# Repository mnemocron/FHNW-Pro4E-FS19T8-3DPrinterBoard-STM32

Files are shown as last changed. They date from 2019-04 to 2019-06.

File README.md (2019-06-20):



# FHNW-Pro4E-FS19T8-3DPrinterBoard-STM32

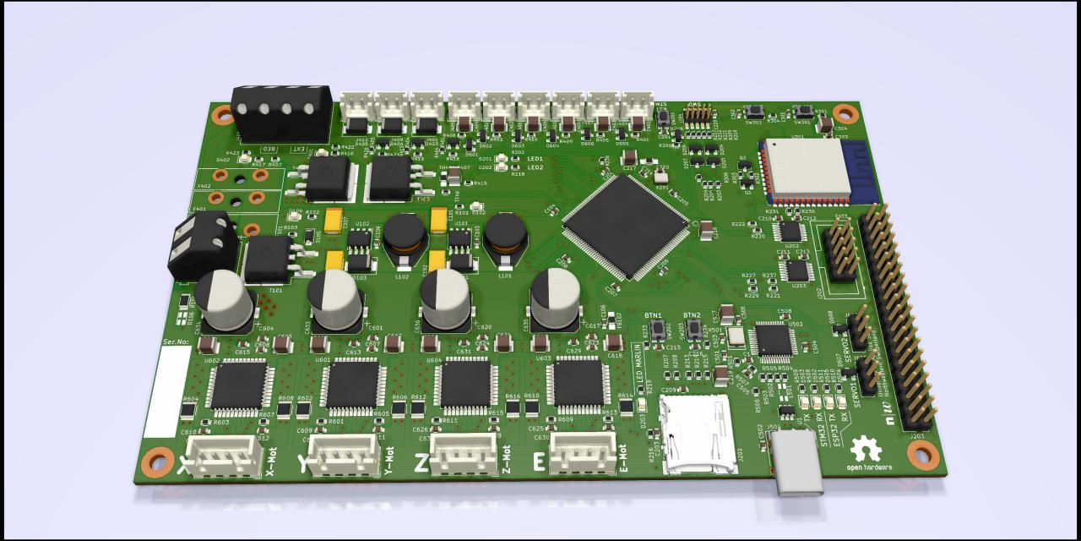
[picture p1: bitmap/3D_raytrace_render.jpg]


Marlin 2.0 compatible 3D printer board based on STM32F103.
Made for the Creality Ender 3 Pro mechanical frame.
Uses TMC2660 with StallGuard for sensorless homing on X and Y axis.

---

volkswagen status (https://github.com/auchenberg/volkswagen)

FHNW School of Engineering

Elektro- und Informationstechnik (EIT)

FS 2019 - Projekt 4 - Team 8

#### Abstract

> This report documents the development of a controller board and the adaptation of an open source ﬁrmware for a common hobbyist 3D printer. The innovative aspects of this hard- and software development are the usage of a 32-bit microcontroller as well as implementing a web interface for remote access. Part of the research included the incorporation of high-end stepper motor drivers, which detect a motor stall, thereby enabling a sensorless homing of the printer’s axes. A Creality Ender 3 Pro provided the mechanical elements of the printer hardware. The mainboard was built around an STM32F103 microcontroller with an ARM Cortex-M3 core.
TMC2660 drivers were used to drive the motors of the three axes (x, y, z) as well as the extruder. Furthermore, Wi-Fi compatibility was achieved by embedding an ESP32-WROOM-32 module on the mainboard. Every feature of the 3D printer, including the upload of G-code ﬁles, can be controlled through the ESP3D ﬁrmware, which provides a web interface. Since the main processor uses a 32-bit architecture, the development branch of the Marlin ﬁrmware 2.0 was used. Additionally, the newly implemented over-the-air update feature can be used to conveniently upload the latest version of the Marlin ﬁrmware to the microcontroller. The use of the stall detection feature of the TMC2660 motor drivers proved to be feasible in order to omit mechanical limit switches on the x- and y-axis. On the z-axis, however, the stall detection feature showed to be too unreliable. Finally, the Marlin 2.0 ﬁrmware is in a working state
and the use of 32-bit microcontrollers is recommended for future developments of 3D printer hardware.

#### Keywords
> 3D printer ﬁrmware, Wi-Fi web interface, sensorless homing, motor stall detection, over-the-air update, Ender 3 Pro, StallGuard

STM32Logo

Based on the `stm32 stm32F103ZEt6`

---

## 💾 Marlin Firmware

Marlin 2.0 Software is in a separate repository.

[MuellerDominik/Marlin](https://github.com/MuellerDominik/Marlin)

---

## 📖 Documentation (German)

Documentation in German is in a seperate repository.

[marco-0909/Pro4_Fachbericht](https://github.com/marco-0909/Pro4_Fachbericht)

---

## ⚠️ Hardware Issues

- wrong Footprint for NPN Transistors in ESP32 reset circuit

The SOT-23 footprint does not match the pinout of the transistor.

- Schematic Error on the LM2675M-x chips

The ON/!OFF pin (pin 5) on both DCDC converters must not be connected to 24V! The pin can only handle 6V. This pin can be left floating.

- The USB type-C receptable can only be soldered using a reflow oven

---

## License

GNU GPLv3

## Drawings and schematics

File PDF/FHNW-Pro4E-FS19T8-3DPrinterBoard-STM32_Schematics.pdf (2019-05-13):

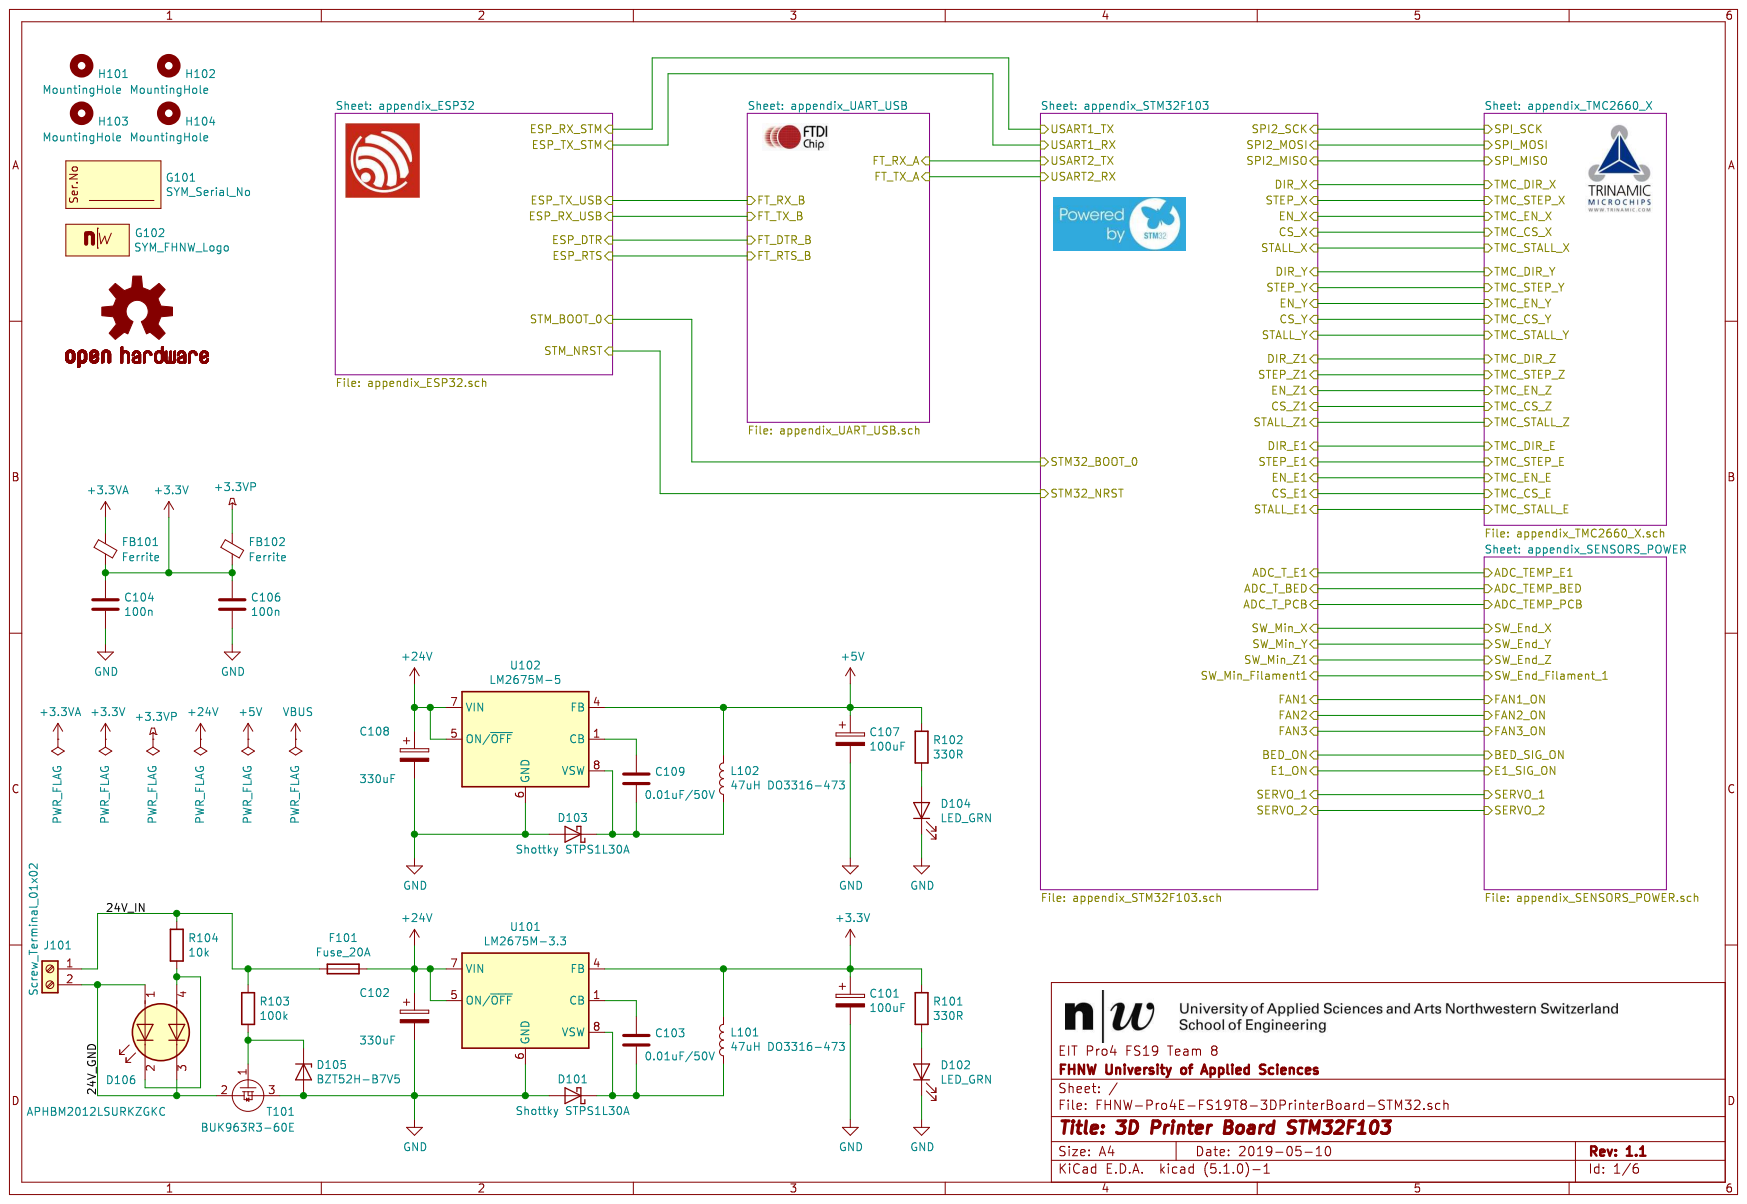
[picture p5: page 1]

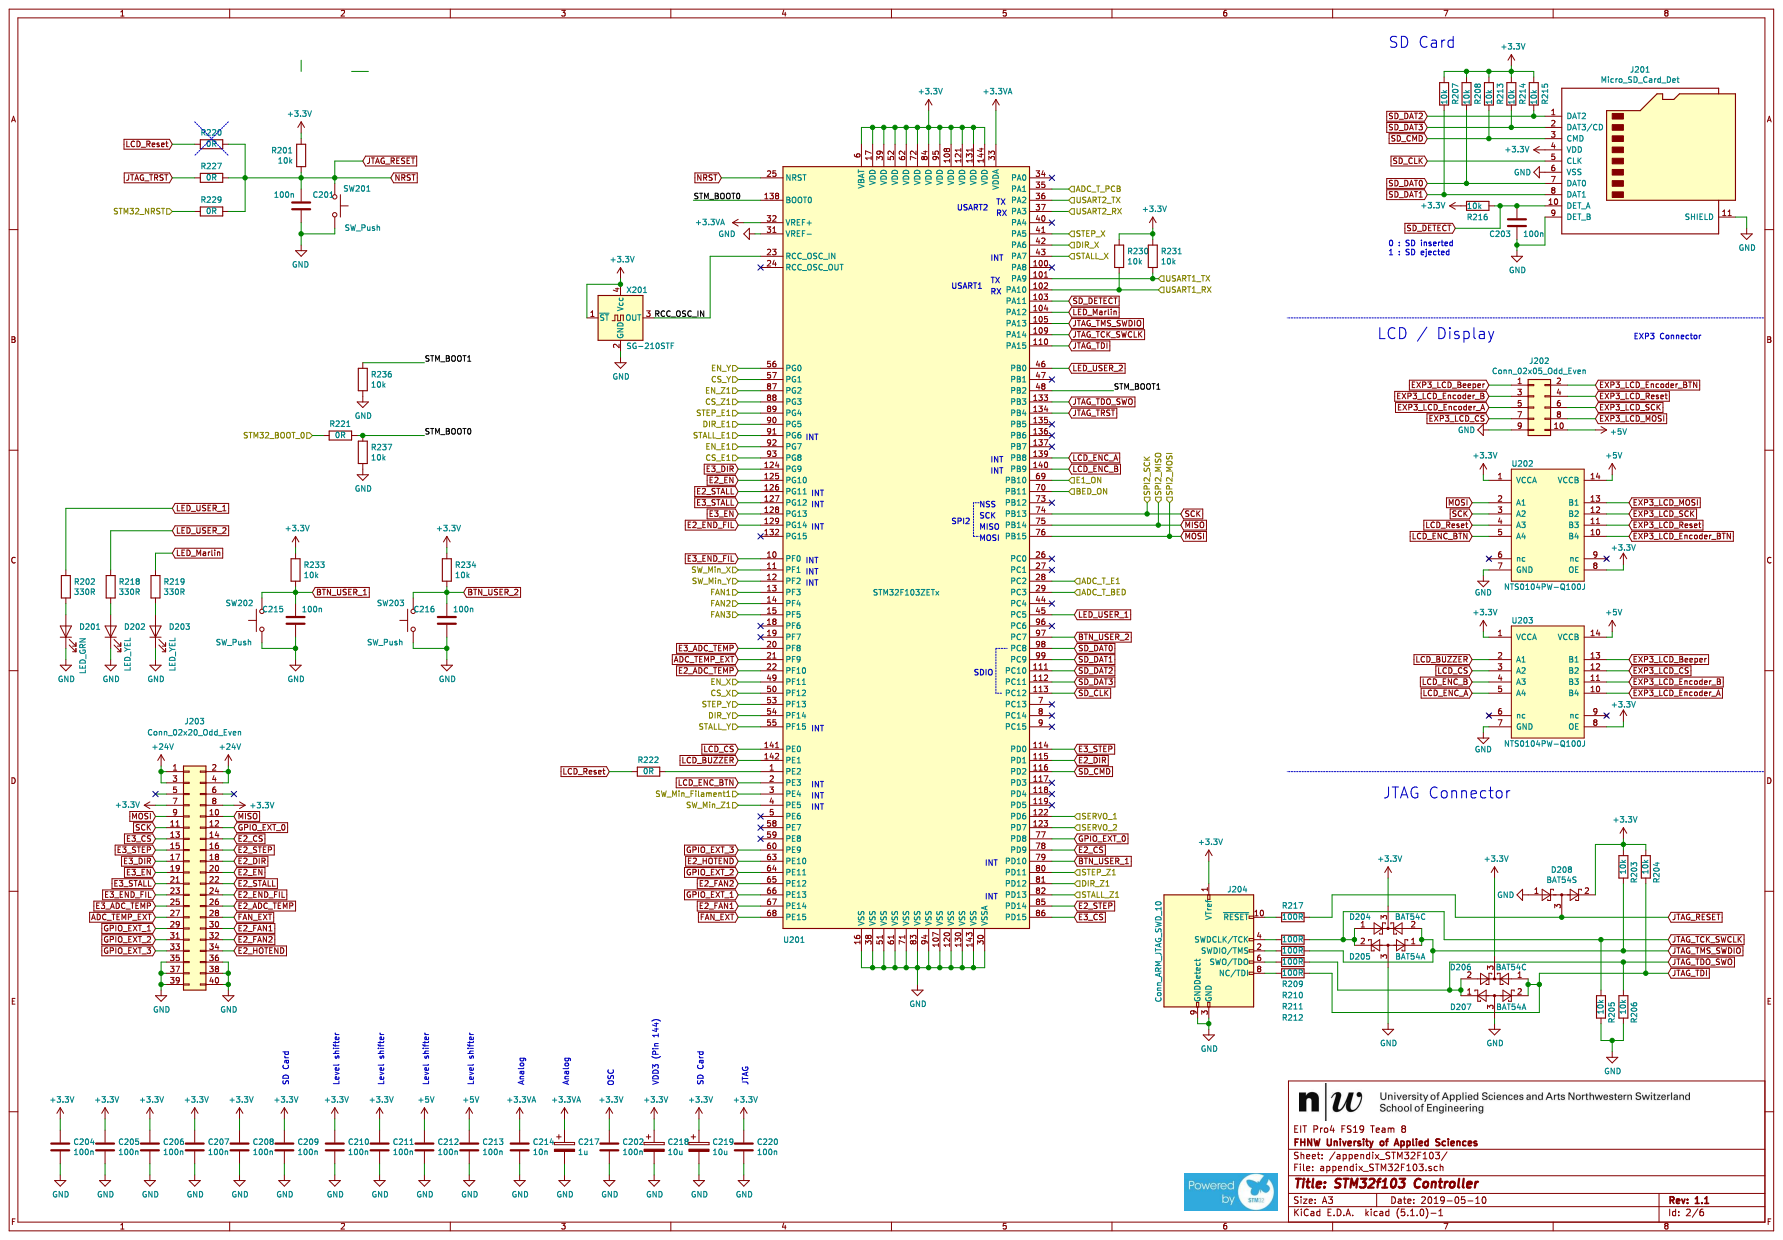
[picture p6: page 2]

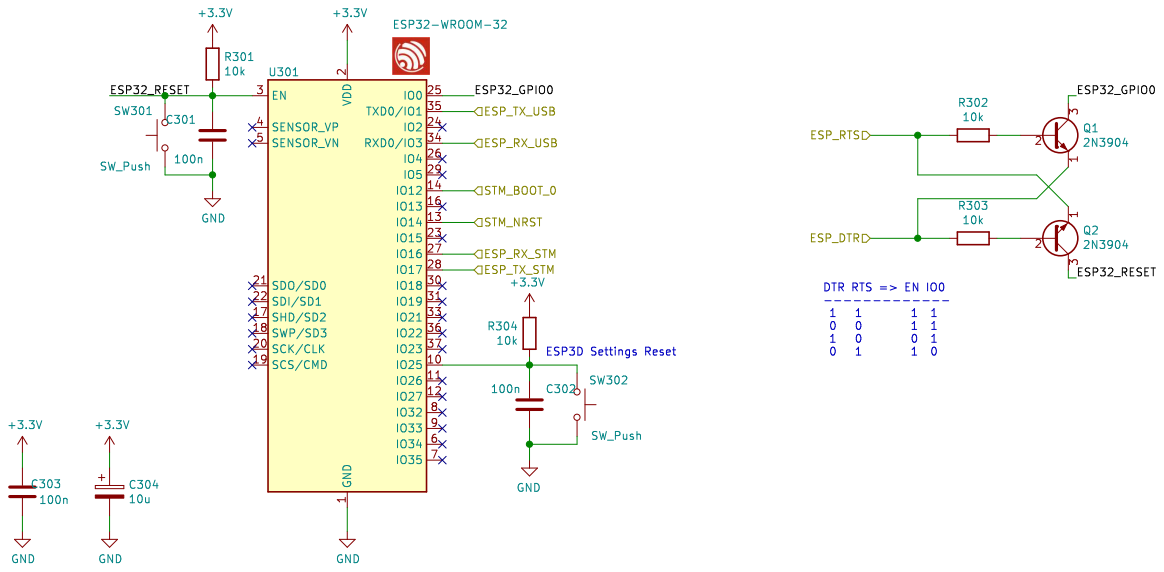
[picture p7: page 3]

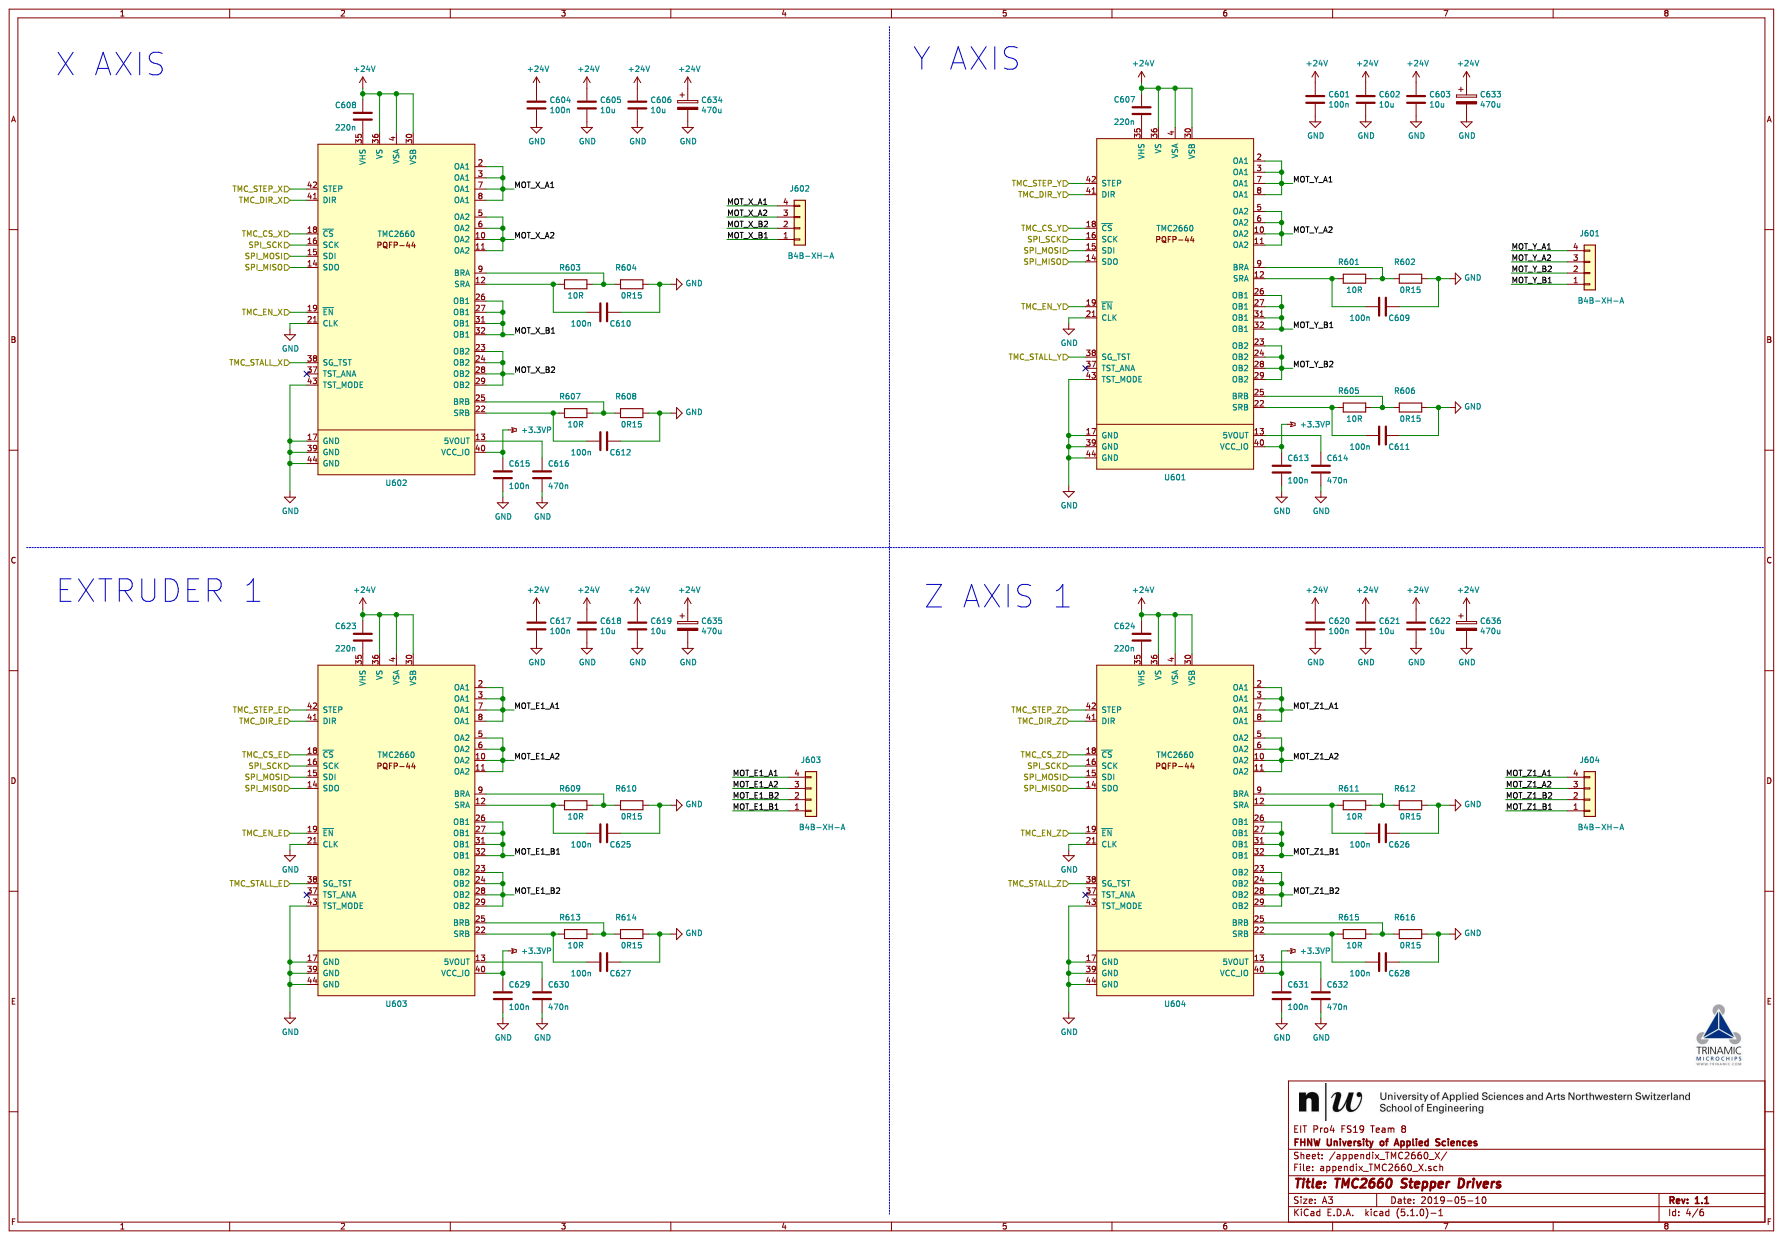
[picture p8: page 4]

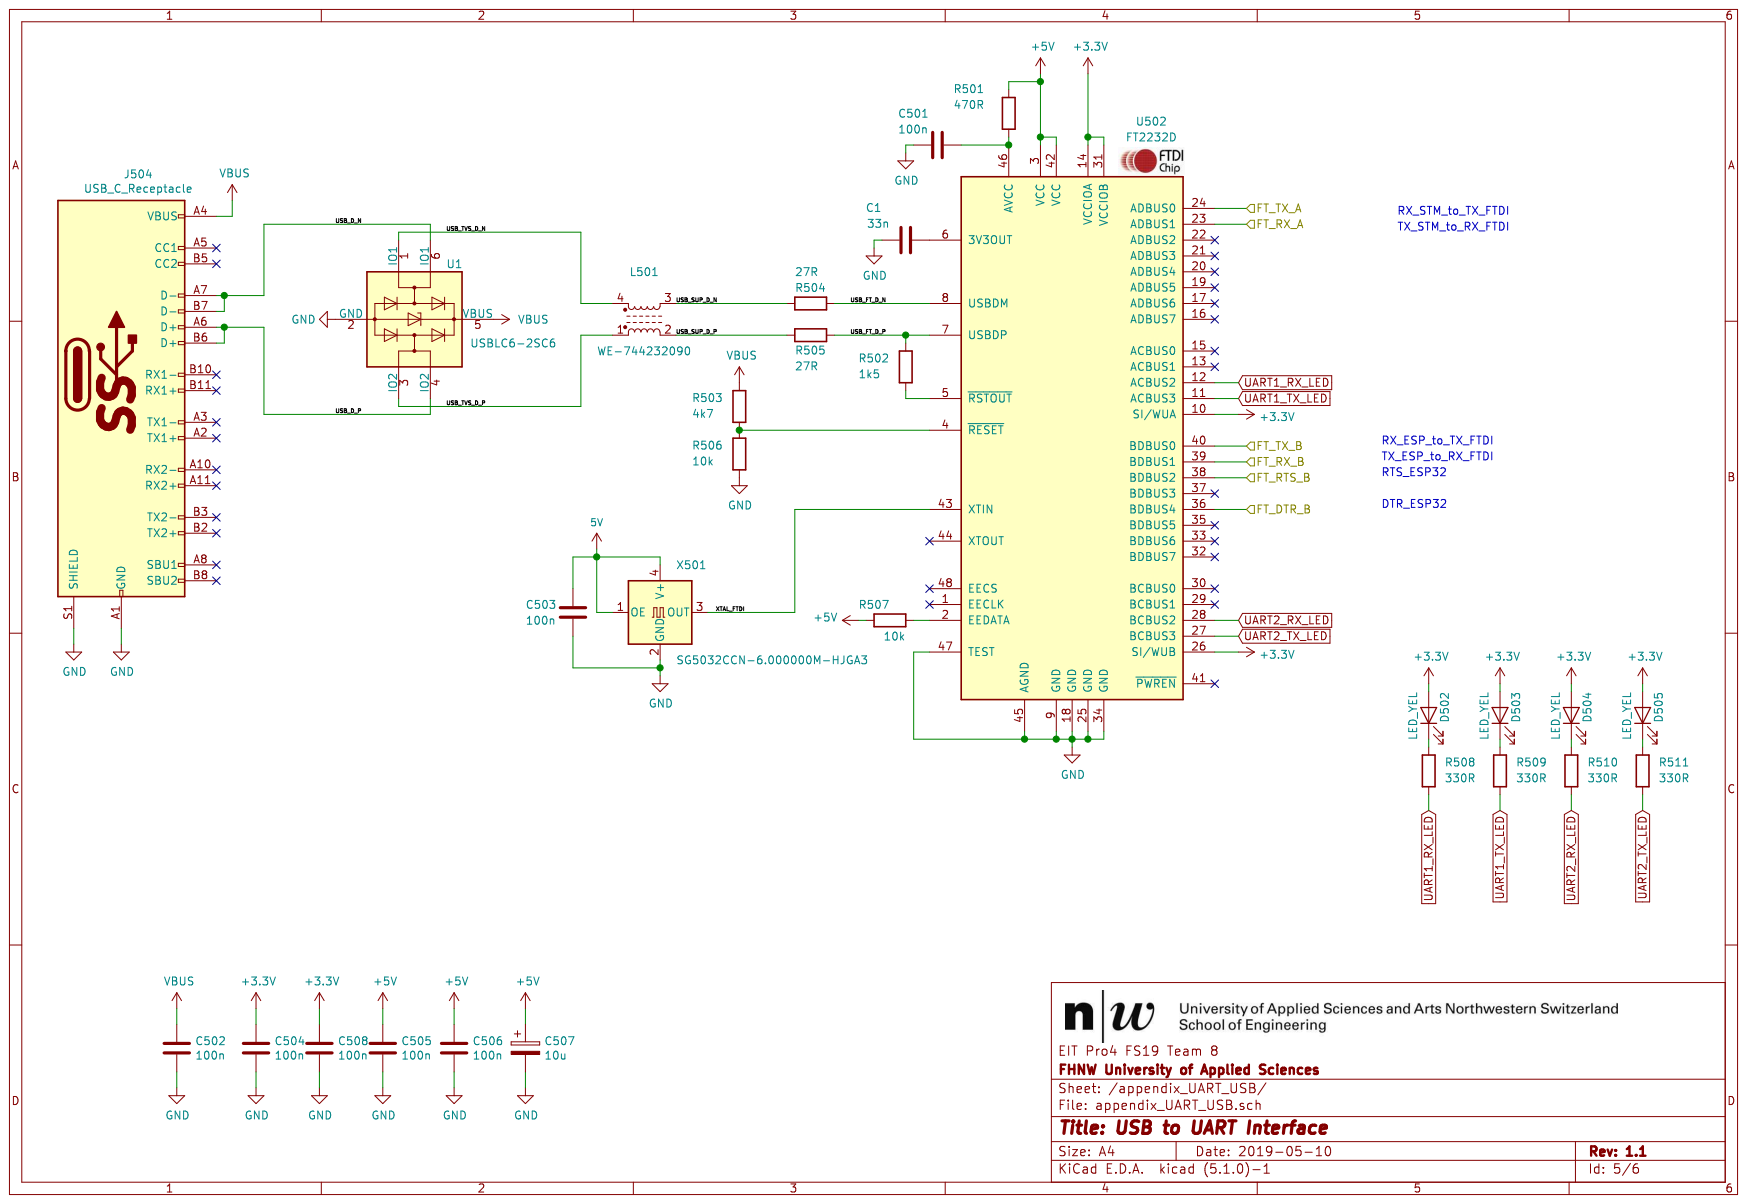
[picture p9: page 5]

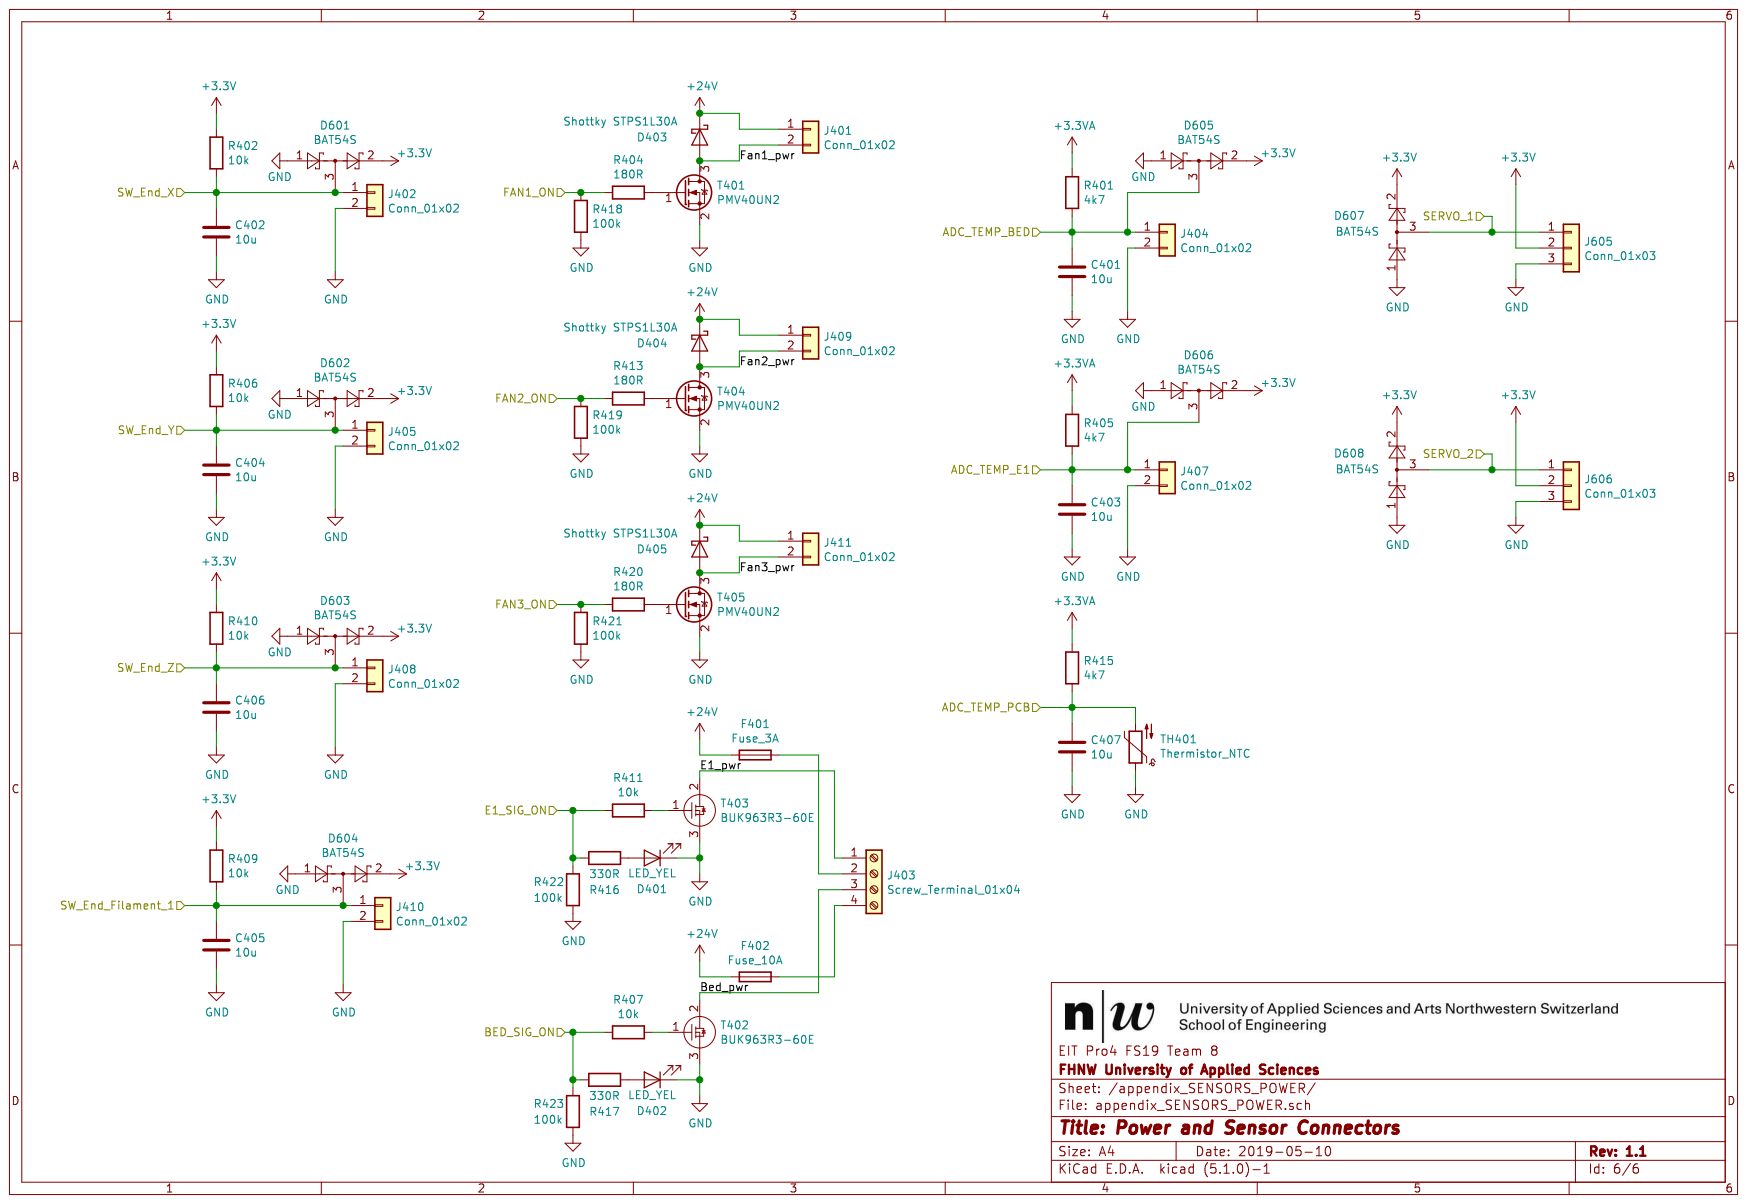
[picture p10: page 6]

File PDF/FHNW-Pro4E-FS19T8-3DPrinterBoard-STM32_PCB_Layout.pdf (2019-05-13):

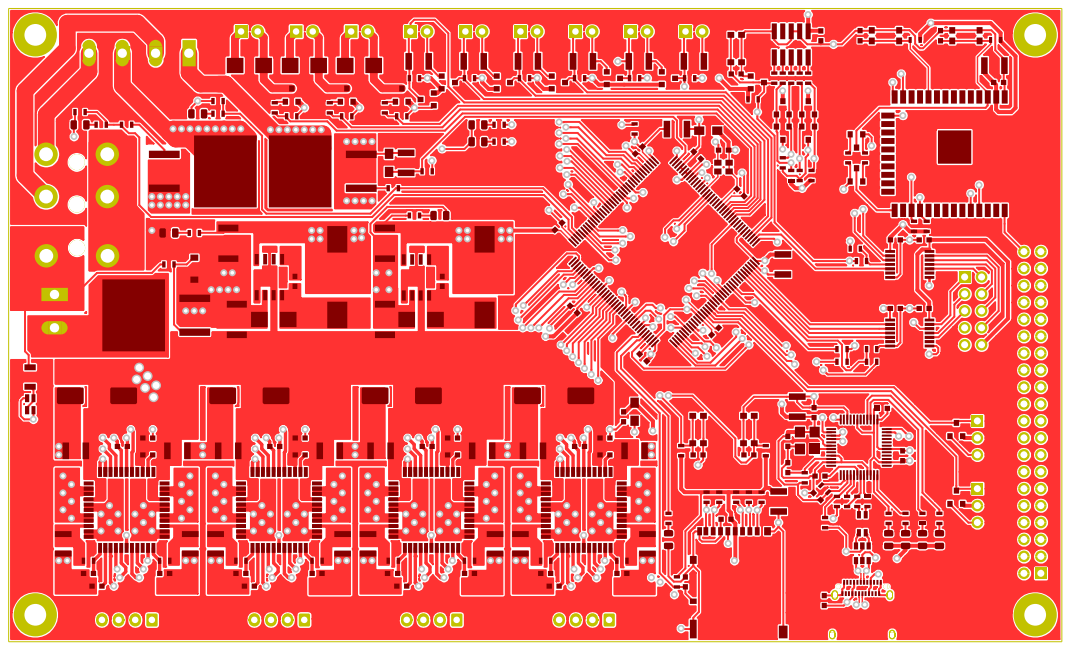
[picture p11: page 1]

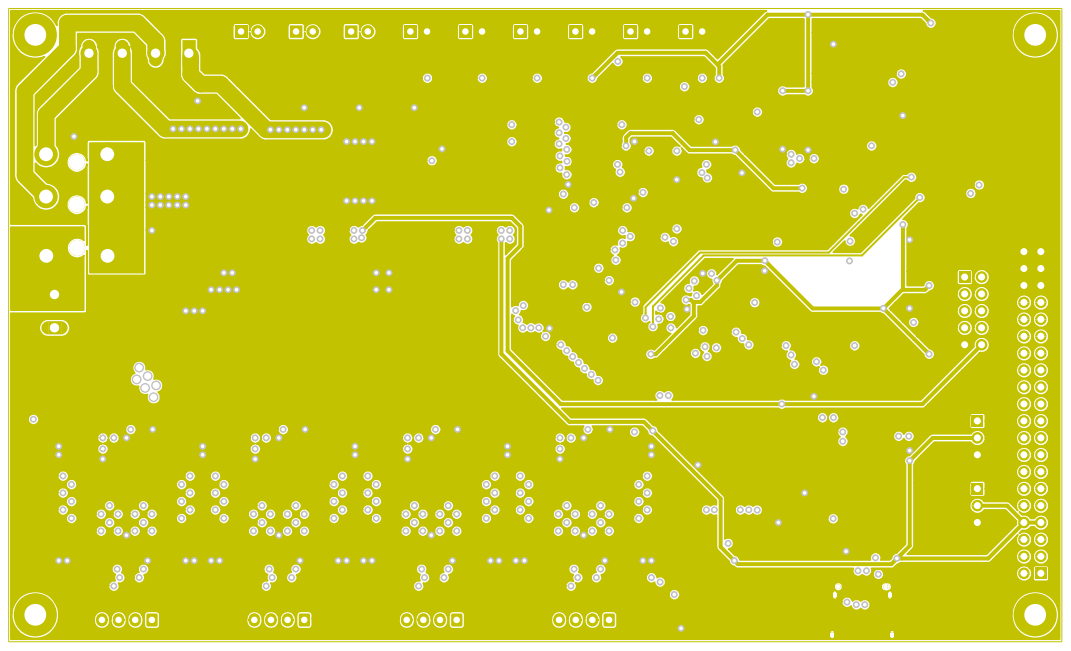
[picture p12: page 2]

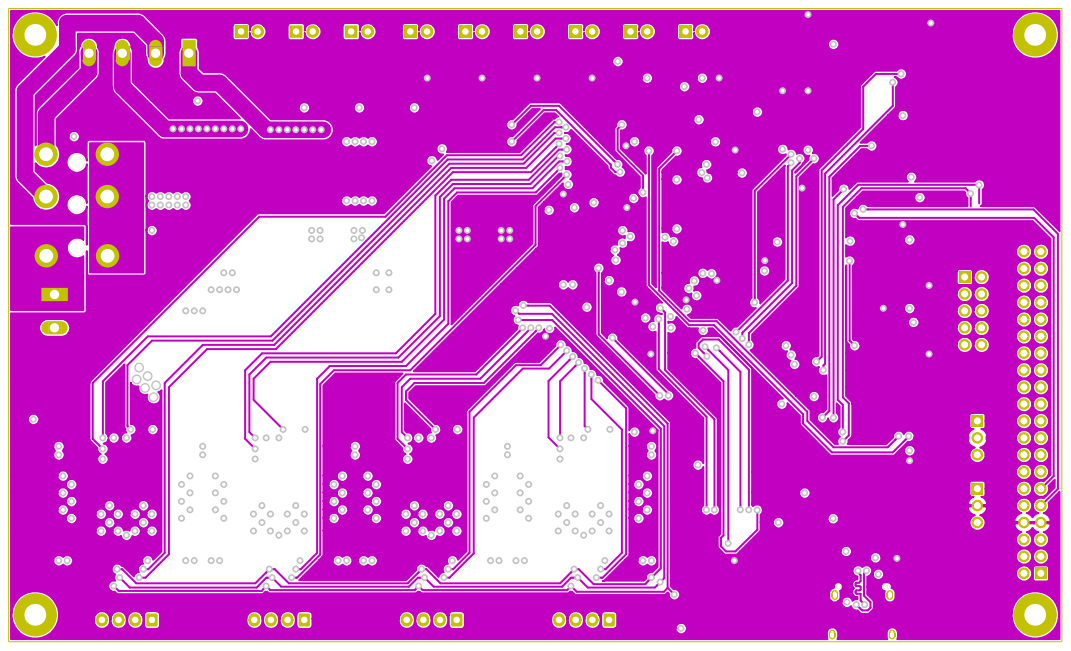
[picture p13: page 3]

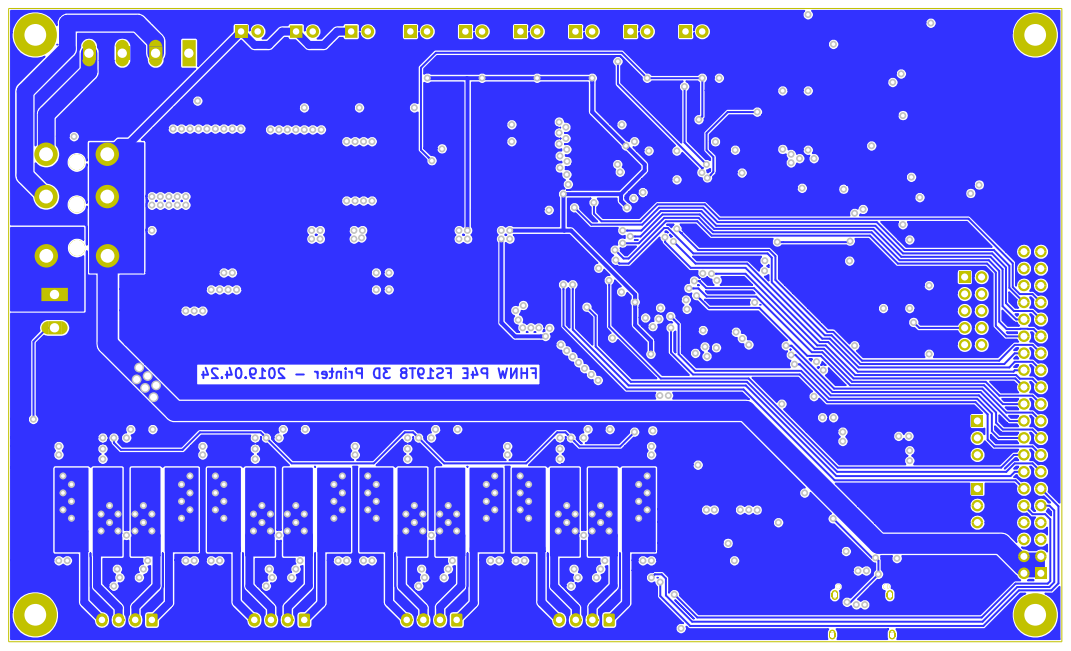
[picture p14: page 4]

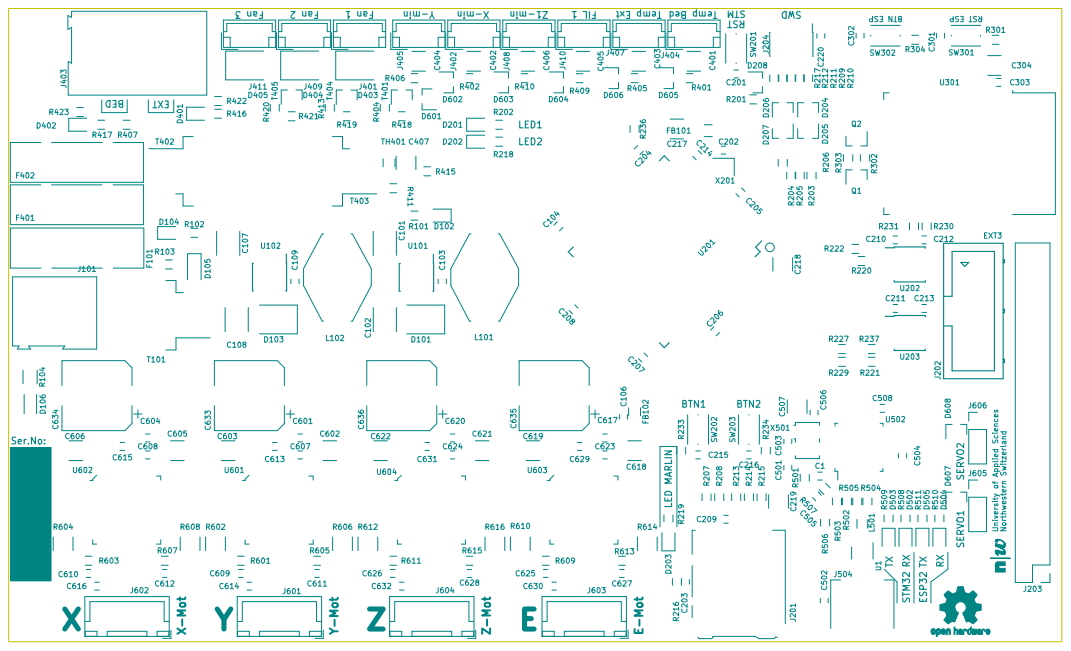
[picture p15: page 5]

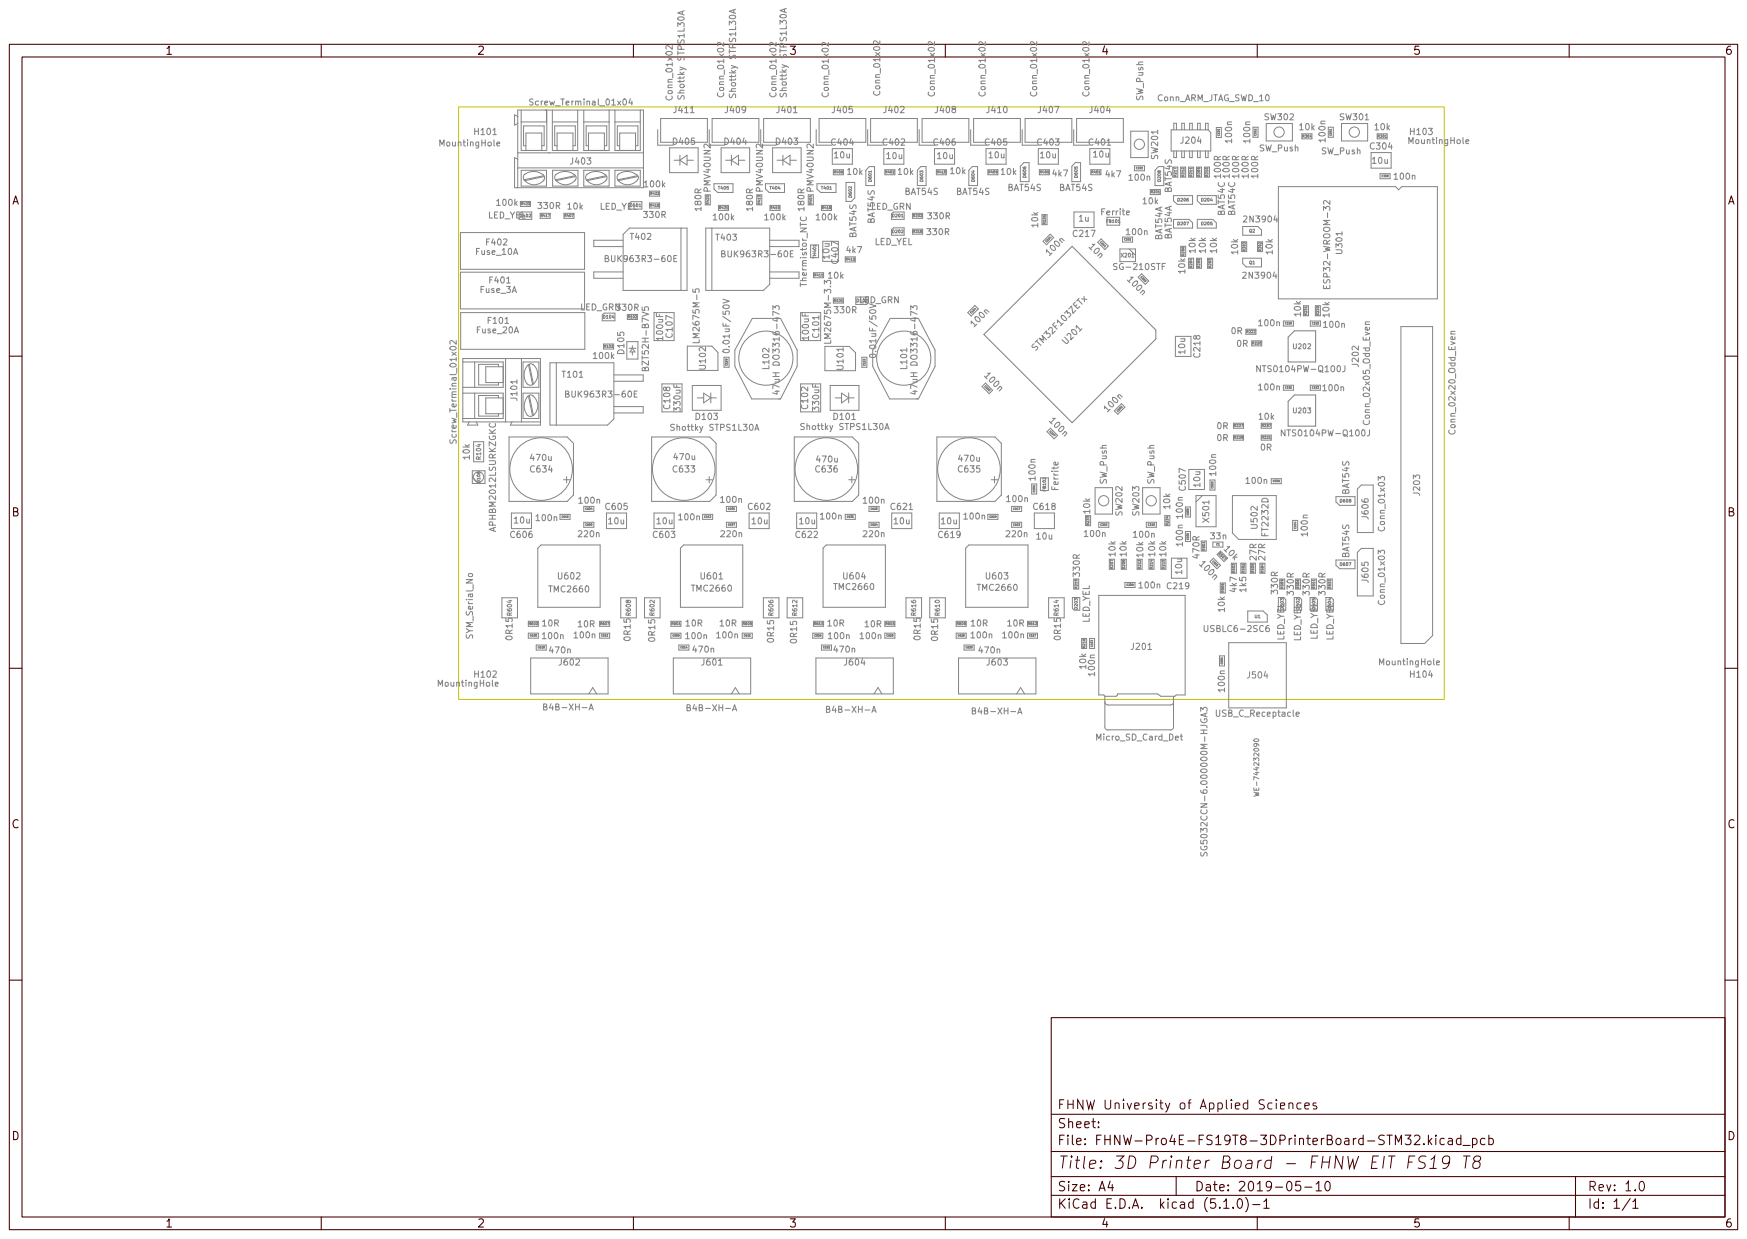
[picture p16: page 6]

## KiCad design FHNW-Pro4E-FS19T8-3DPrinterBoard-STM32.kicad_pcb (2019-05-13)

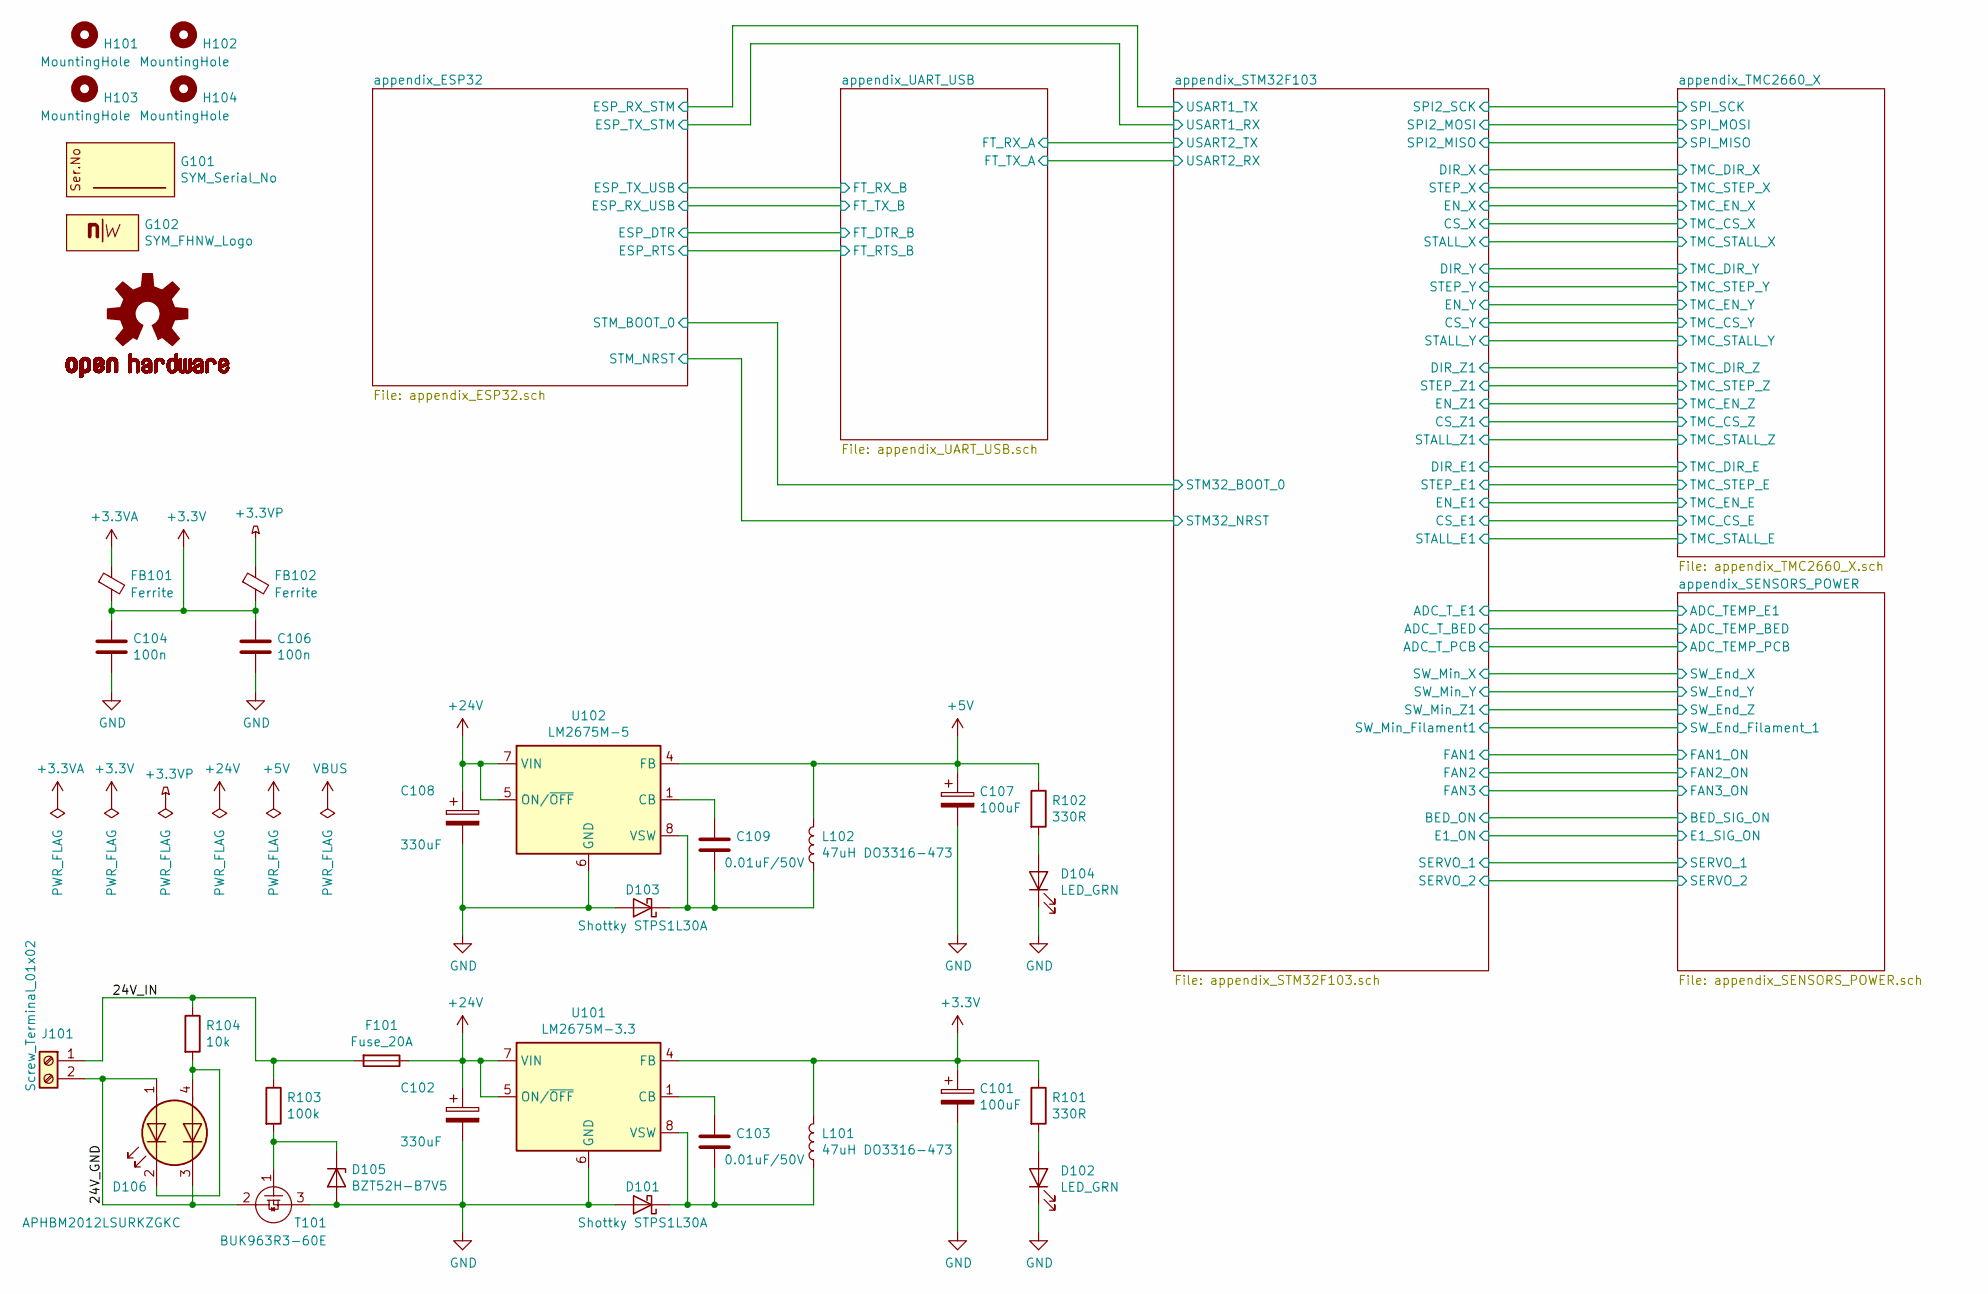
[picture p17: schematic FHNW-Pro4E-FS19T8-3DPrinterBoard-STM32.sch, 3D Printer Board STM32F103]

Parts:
C101, C107: 100uF; C_1812
C102, C108: 330uF; C_1812
C103, C109: 0.01uF/50V; C_0603
C104, C106: 100n; C_0603
D101, D103: Shottky STPS1L30A; D_SMB
D102, D104: LED_GRN; LED_0805_2012Metric
D105: BZT52H-B7V5; D_SOD-123
D106: APHBM2012LSURKZGKC; LED_Kingbright_SMD4_2.0x1.25
F101: Fuse_20A; Fuseholder_Blade_ATO_Littelfuse_Pudenz_2_Pin
FB101, FB102: Ferrite; R_0805_HandSoldering
G101: SYM_Serial_No; Label_Serial_Number_6x20
G102: SYM_FHNW_Logo; Logo_FHNW_03x05mm
H101, H102, H103, H104: MountingHole; MountingHole_3.2mm_M3_Pad
J101: Screw_Terminal_01x02; TerminalBlock_Altech_AK300-2_P5.00mm
L101, L102: 47uH DO3316-473; L_Fastron_PISN_Handsoldering
LOGO101: OSHW-LOGOM-COPPER; OSHW-Logo2_9.8x8mm_SilkScreen
R101, R102: 330R; R_0603
R103: 100k; R_0603
R104: 10k; R_1206
T101: BUK963R3-60E; TO-263-2
U101: LM2675M-3.3; SOIC-8_3.9x4.9mm_P1.27mm
U102: LM2675M-5; SOIC-8_3.9x4.9mm_P1.27mm

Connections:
+3.3VA: FB101.1; also elsewhere on the board
+3.3VP: FB102.1; also elsewhere on the board
+3V3: C101.1, C104.1, C106.1, FB101.2, FB102.2, L101.2, R101.1, U101.4 (FB); also elsewhere on the board
+24V: C102.1, C108.1, F101.1, U101.5 (ON/~OFF), U101.7 (VIN), U102.5 (ON/~OFF), U102.7 (VIN); also elsewhere on the board
/24V_GND: D106.1 (A1), D106.3 (K2), J101.2, T101.2
/24V_IN: F101.2, J101.1, R103.1, R104.1
GND: C101.2, C102.2, C104.2, C106.2, C107.2, C108.2, D101.2 (A), D102.1 (K), D103.2 (A), D104.1 (K), D105.2 (A), T101.3, U101.6 (GND), U102.6 (GND); also elsewhere on the board
unnamed: C103.1, U101.1 (CB)
unnamed: C103.2, D101.1 (K), L101.1, U101.8 (VSW)
unnamed: C109.1, U102.1 (CB)
unnamed: C109.2, D103.1 (K), L102.1, U102.8 (VSW)
unnamed: D102.2 (A), R101.2
unnamed: D104.2 (A), R102.2
unnamed: D105.1 (K), R103.2, T101.1
unnamed: D106.2 (K1), D106.4 (A2), R104.2

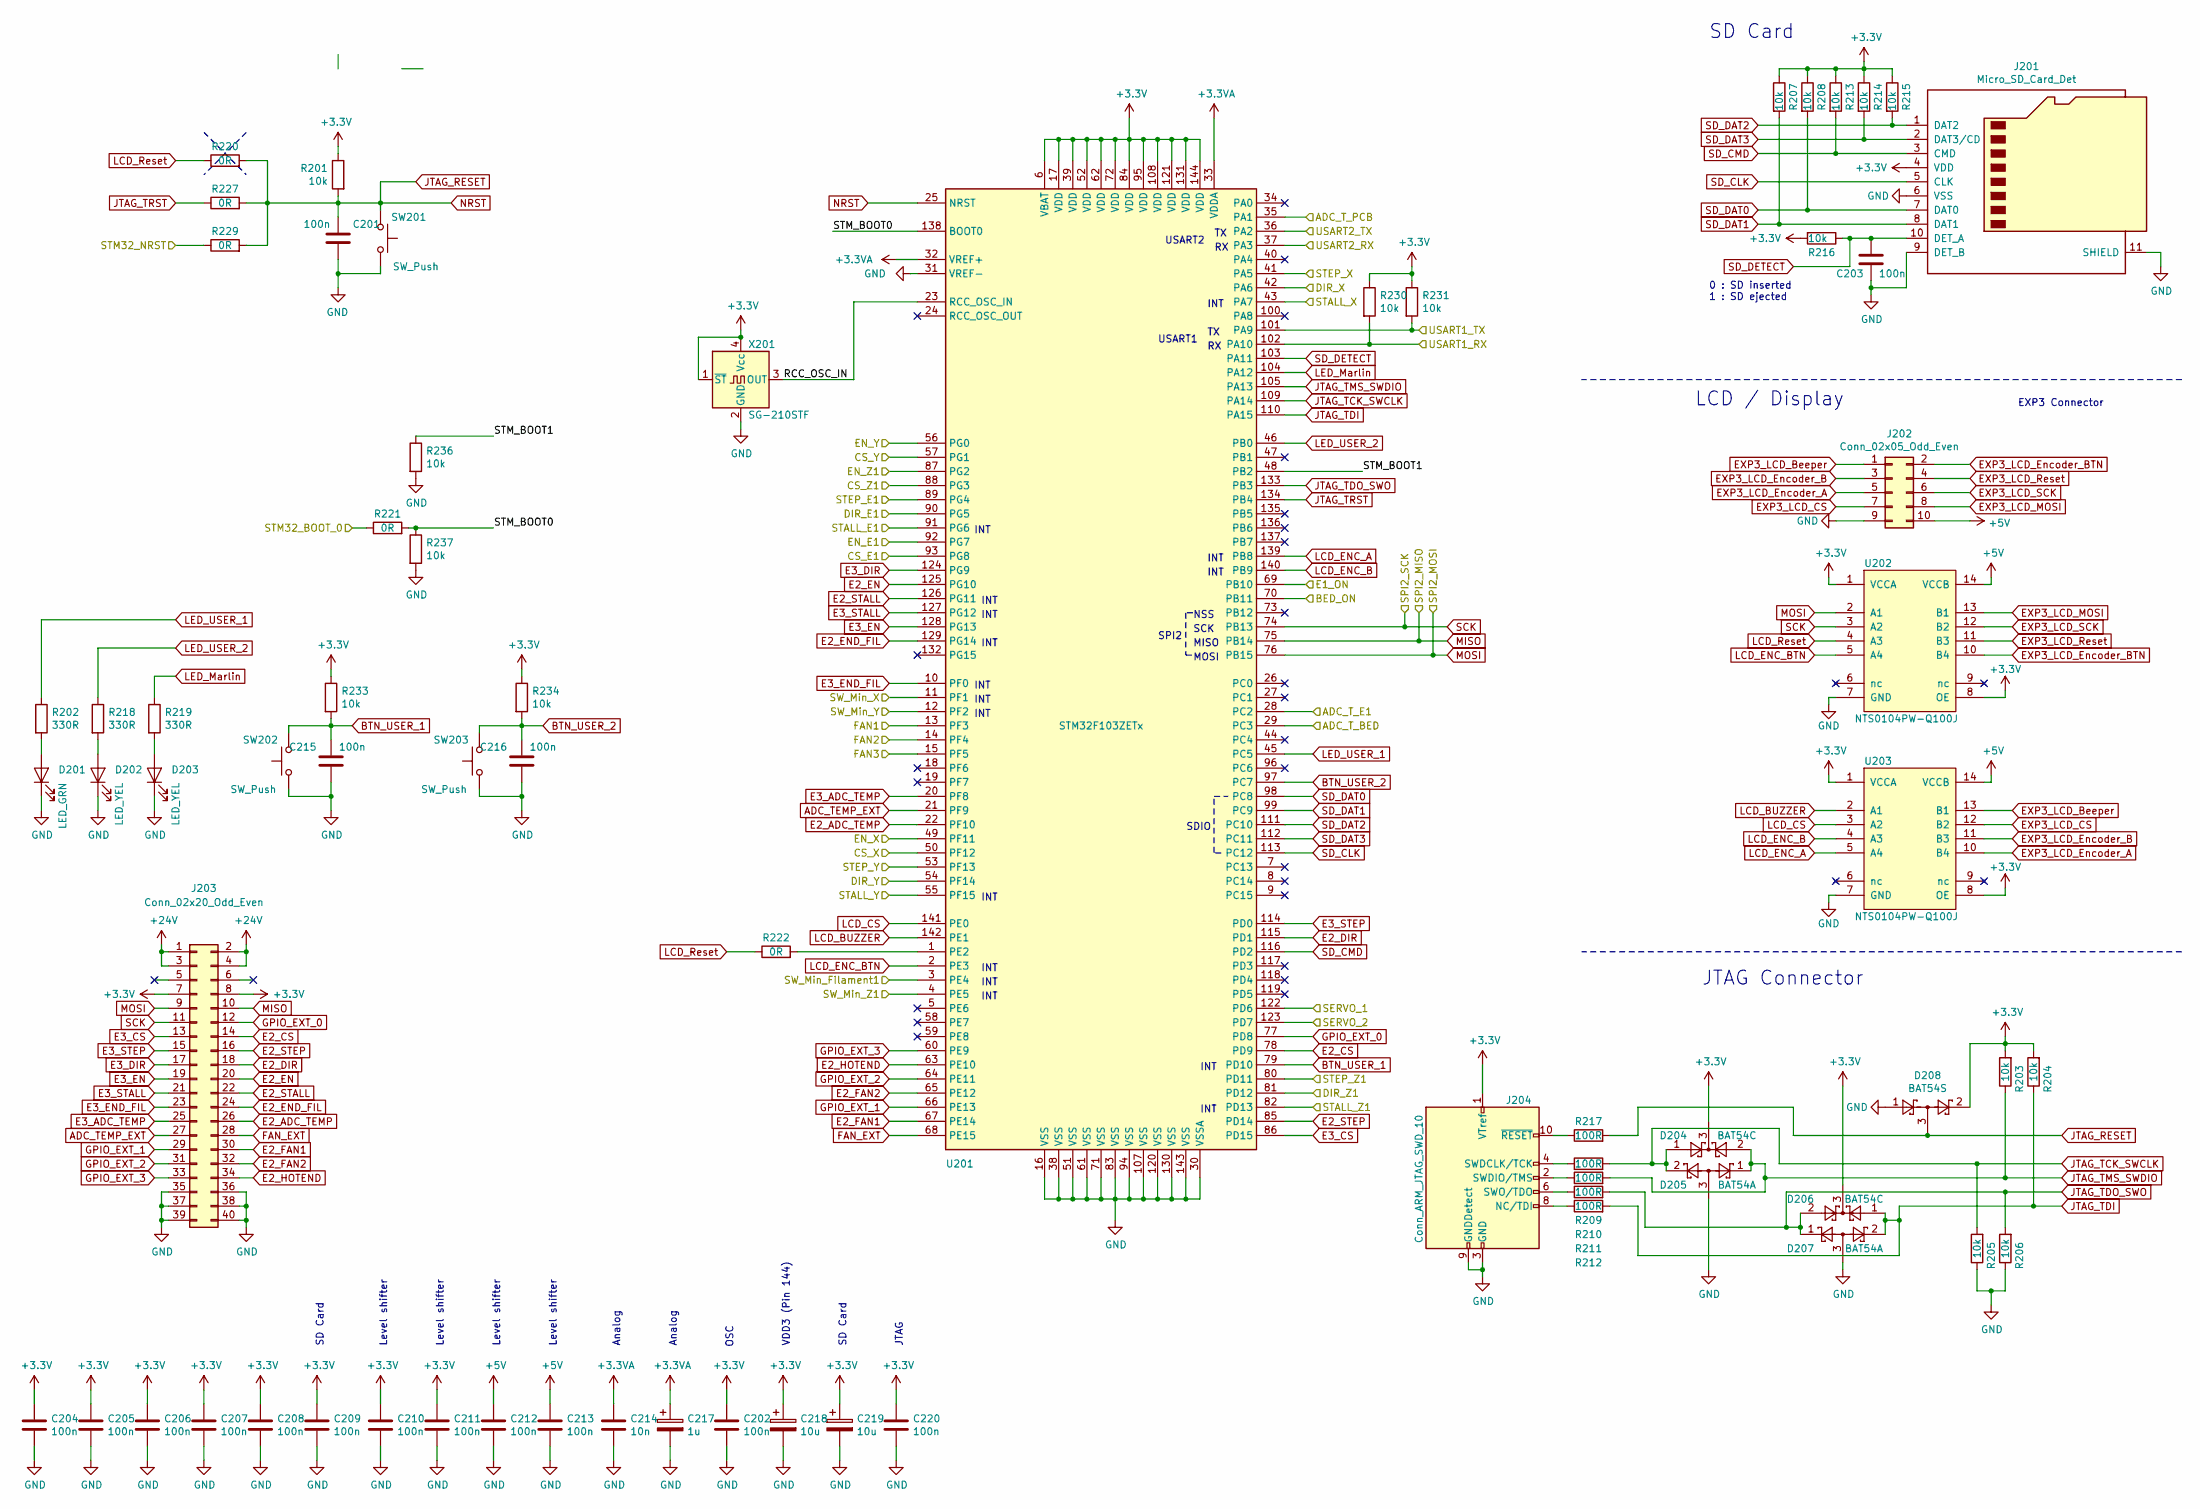
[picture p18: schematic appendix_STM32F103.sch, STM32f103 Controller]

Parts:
C201, C202, C203, C204, C205, C206, C207, C208, C209, C210, C211, C212, C213, C215, C216, C220: 100n; C_0603
C214: 10n; C_0603
C217: 1u; C_1210
C218, C219: 10u; C_1210
D201: LED_GRN; LED_0805_2012Metric
D202, D203: LED_YEL; LED_0805_2012Metric
D204, D206: BAT54C; SOT-23
D205, D207: BAT54A; SOT-23
D208: BAT54S; SOT-23
J201: Micro_SD_Card_Det; microSD_HC_Hirose_DM3AT-SF-PEJM5
J202: Conn_02x05_Odd_Even; Multicomp_MC9A12-1034_2x05_P2.54mm_Vertical
J203: Conn_02x20_Odd_Even; PinHeader_2x20_P2.54mm_Vertical
J204: Conn_ARM_JTAG_SWD_10; PinHeader_2x05_P1.27mm_Vertical_SMD
R201, R203, R204, R205, R206, R207, R208, R213, R214, R215, R216, R230, R231, R233, R234, R236, R237: 10k; R_0603
R202, R218, R219: 330R; R_0603
R209, R210, R211, R212, R217: 100R; R_0603
R220, R221, R222, R227, R229: 0R; R_0603
SW201, SW202, SW203: SW_Push; SW_SPST_KMR2
U201: STM32F103ZETx; LQFP-144_20x20mm_Pitch0.5mm
U202, U203: NTS0104PW-Q100J; TSSOP-14_4.4x5mm_Pitch0.65mm
X201: SG-210STF; Oscillator_SMD_SeikoEpson_SG210-4Pin_2.5x2.0mm

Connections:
+3.3VA: C214.1, C217.1, U201.32 (VREF+), U201.33 (VDDA); also elsewhere on the board
+3V3: C202.1, C204.1, C205.1, C206.1, C207.1, C208.1, C209.1, C210.1, C211.1, C218.1, C219.1, C220.1, D204.3, D206.3, D208.2, J201.4 (VDD), J203.7, J203.8, J204.1 (VTref), R201.1, R203.2, R204.2, R207.1, R208.1, R213.1, R214.1, R215.1, R216.2, R230.1, R231.1, R233.1, R234.1, U201.6 (VBAT), U201.17 (VDD), U201.39 (VDD), U201.52 (VDD), U201.62 (VDD), U201.72 (VDD), U201.84 (VDD), U201.95 (VDD), U201.108 (VDD), U201.121 (VDD), U201.131 (VDD), U201.144 (VDD), U202.1 (VCCA), U202.8 (OE), U203.1 (VCCA), U203.8 (OE), X201.1 (~ST~), X201.4 (Vcc); also elsewhere on the board
+24V: J203.1, J203.2, J203.3, J203.4; also elsewhere on the board
/appendix_ESP32/ESP_RX_STM: R231.2, U201.101 (PA9); also elsewhere on the board
/appendix_ESP32/ESP_TX_STM: R230.2, U201.102 (PA10); also elsewhere on the board
/appendix_SENSORS_POWER/ADC_TEMP_BED: U201.29 (PC3); also elsewhere on the board
/appendix_SENSORS_POWER/ADC_TEMP_E1: U201.28 (PC2); also elsewhere on the board
/appendix_SENSORS_POWER/ADC_TEMP_PCB: U201.35 (PA1); also elsewhere on the board
/appendix_SENSORS_POWER/SERVO_1: U201.122 (PD6); also elsewhere on the board
/appendix_SENSORS_POWER/SERVO_2: U201.123 (PD7); also elsewhere on the board
/appendix_SENSORS_POWER/SW_End_Filament_1: U201.3 (PE4); also elsewhere on the board
/appendix_SENSORS_POWER/SW_End_X: U201.11 (PF1); also elsewhere on the board
/appendix_SENSORS_POWER/SW_End_Y: U201.12 (PF2); also elsewhere on the board
/appendix_SENSORS_POWER/SW_End_Z: U201.4 (PE5); also elsewhere on the board
/appendix_STM32F103/BED_ON: U201.70 (PB11); also elsewhere on the board
/appendix_STM32F103/CS_E1: U201.93 (PG8); also elsewhere on the board
/appendix_STM32F103/CS_X: U201.50 (PF12); also elsewhere on the board
/appendix_STM32F103/CS_Y: U201.57 (PG1); also elsewhere on the board
/appendix_STM32F103/CS_Z1: U201.88 (PG3); also elsewhere on the board
/appendix_STM32F103/DIR_E1: U201.90 (PG5); also elsewhere on the board
/appendix_STM32F103/DIR_X: U201.42 (PA6); also elsewhere on the board
/appendix_STM32F103/DIR_Y: U201.54 (PF14); also elsewhere on the board
/appendix_STM32F103/DIR_Z1: U201.81 (PD12); also elsewhere on the board
/appendix_STM32F103/E1_ON: U201.69 (PB10); also elsewhere on the board
/appendix_STM32F103/EN_E1: U201.92 (PG7); also elsewhere on the board
/appendix_STM32F103/EN_X: U201.49 (PF11); also elsewhere on the board
/appendix_STM32F103/EN_Y: U201.56 (PG0); also elsewhere on the board
/appendix_STM32F103/EN_Z1: U201.87 (PG2); also elsewhere on the board
/appendix_STM32F103/FAN1: U201.13 (PF3); also elsewhere on the board
/appendix_STM32F103/FAN2: U201.14 (PF4); also elsewhere on the board
/appendix_STM32F103/FAN3: U201.15 (PF5); also elsewhere on the board
/appendix_STM32F103/RCC_OSC_IN: U201.23 (RCC_OSC_IN), X201.3 (OUT)
/appendix_STM32F103/STALL_E1: U201.91 (PG6); also elsewhere on the board
/appendix_STM32F103/STALL_X: U201.43 (PA7); also elsewhere on the board
/appendix_STM32F103/STALL_Y: U201.55 (PF15); also elsewhere on the board
/appendix_STM32F103/STALL_Z1: U201.82 (PD13); also elsewhere on the board
/appendix_STM32F103/STEP_E1: U201.89 (PG4); also elsewhere on the board
/appendix_STM32F103/STEP_X: U201.41 (PA5); also elsewhere on the board
/appendix_STM32F103/STEP_Y: U201.53 (PF13); also elsewhere on the board
/appendix_STM32F103/STEP_Z1: U201.80 (PD11); also elsewhere on the board
/appendix_STM32F103/STM32_BOOT_0: R221.1; also elsewhere on the board
/appendix_STM32F103/STM32_NRST: R229.1; also elsewhere on the board
/appendix_STM32F103/STM_BOOT0: R221.2, R237.1, U201.138 (BOOT0)
/appendix_STM32F103/STM_BOOT1: R236.1, U201.48 (PB2)
/appendix_UART_USB/FT_RX_A: U201.36 (PA2); also elsewhere on the board
/appendix_UART_USB/FT_TX_A: U201.37 (PA3); also elsewhere on the board
ADC_TEMP_EXT: J203.27, U201.21 (PF9)
BTN_USER_1: C215.1, R233.2, SW202.2, U201.79 (PD10)
BTN_USER_2: C216.1, R234.2, SW203.2, U201.97 (PC7)
E2_ADC_TEMP: J203.26, U201.22 (PF10)
E2_CS: J203.14, U201.78 (PD9)
E2_DIR: J203.18, U201.115 (PD1)
E2_EN: J203.20, U201.125 (PG10)
E2_END_FIL: J203.24, U201.129 (PG14)
E2_FAN1: J203.30, U201.67 (PE14)
E2_FAN2: J203.32, U201.65 (PE12)
E2_HOTEND: J203.34, U201.63 (PE10)
E2_STALL: J203.22, U201.126 (PG11)
E2_STEP: J203.16, U201.85 (PD14)
E3_ADC_TEMP: J203.25, U201.20 (PF8)
E3_CS: J203.13, U201.86 (PD15)
E3_DIR: J203.17, U201.124 (PG9)
E3_EN: J203.19, U201.128 (PG13)
E3_END_FIL: J203.23, U201.10 (PF0)
E3_STALL: J203.21, U201.127 (PG12)
E3_STEP: J203.15, U201.114 (PD0)
EXP3_LCD_Beeper: J202.1, U203.13 (B1)
EXP3_LCD_CS: J202.7, U203.12 (B2)
EXP3_LCD_Encoder_A: J202.5, U203.10 (B4)
EXP3_LCD_Encoder_B: J202.3, U203.11 (B3)
EXP3_LCD_Encoder_BTN: J202.2, U202.10 (B4)
EXP3_LCD_MOSI: J202.8, U202.13 (B1)
EXP3_LCD_Reset: J202.4, U202.11 (B3)
EXP3_LCD_SCK: J202.6, U202.12 (B2)
FAN_EXT: J203.28, U201.68 (PE15)
GND: C201.2, C202.2, C203.2, C204.2, C205.2, C206.2, C207.2, C208.2, C209.2, C210.2, C211.2, C212.2, C213.2, C214.2, C215.2, C216.2, C217.2, C218.2, C219.2, C220.2, D201.1 (K), D202.1 (K), D203.1 (K), D205.3, D207.3, D208.1, J201.6 (VSS), J201.9 (DET_B), J201.11 (SHIELD), J202.9, J203.35, J203.36, J203.37, J203.38, J203.39, J203.40, J204.3 (GND), J204.5 (GND), J204.9 (GNDDetect), R205.1, R206.1, R236.2, R237.2, SW201.1, SW202.1, SW203.1, U201.16 (VSS), U201.30 (VSSA), U201.31 (VREF-), U201.38 (VSS), U201.51 (VSS), U201.61 (VSS), U201.71 (VSS), U201.83 (VSS), U201.94 (VSS), U201.107 (VSS), U201.120 (VSS), U201.130 (VSS), U201.143 (VSS), U202.7 (GND), U203.7 (GND), X201.2 (GND); also elsewhere on the board
GPIO_EXT_0: J203.12, U201.77 (PD8)
GPIO_EXT_1: J203.29, U201.66 (PE13)
GPIO_EXT_2: J203.31, U201.64 (PE11)
GPIO_EXT_3: J203.33, U201.60 (PE9)
JTAG_RESET: C201.1, D208.3, R201.2, R217.2, R220.2, R227.2, R229.2, SW201.2, U201.25 (NRST)
JTAG_TCK_SWCLK: D204.1, D205.2, R205.2, R209.2, U201.109 (PA14)
JTAG_TDI: D206.1, D207.2, R204.1, R212.2, U201.110 (PA15)
JTAG_TDO_SWO: D206.2, D207.1, R206.2, R211.2, U201.133 (PB3)
JTAG_TMS_SWDIO: D204.2, D205.1, R203.1, R210.2, U201.105 (PA13)
JTAG_TRST: R227.1, U201.134 (PB4)
LCD_BUZZER: U201.142 (PE1), U203.2 (A1)
LCD_CS: U201.141 (PE0), U203.3 (A2)
LCD_ENC_A: U201.139 (PB8), U203.5 (A4)
LCD_ENC_B: U201.140 (PB9), U203.4 (A3)
LCD_ENC_BTN: U201.2 (PE3), U202.5 (A4)
LCD_Reset: R220.1, R222.1, U202.4 (A3)
LED_Marlin: R219.1, U201.104 (PA12)
LED_USER_1: R202.1, U201.45 (PC5)
LED_USER_2: R218.1, U201.46 (PB0)
MISO: J203.10, U201.75 (PB14); also elsewhere on the board
MOSI: J203.9, U201.76 (PB15), U202.2 (A1); also elsewhere on the board
unnamed: D201.2 (A), R202.2
unnamed: D202.2 (A), R218.2
unnamed: D203.2 (A), R219.2
unnamed: J204.2 (SWDIO/TMS), R210.1
unnamed: J204.4 (SWDCLK/TCK), R209.1
unnamed: J204.6 (SWO/TDO), R211.1
unnamed: J204.8 (NC/TDI), R212.1
unnamed: J204.10 (~RESET~), R217.1
unnamed: R222.2, U201.1 (PE2)
SCK: J203.11, U201.74 (PB13), U202.3 (A2); also elsewhere on the board
SD_CLK: J201.5 (CLK), U201.113 (PC12)
SD_CMD: J201.3 (CMD), R213.2, U201.116 (PD2)
SD_DAT0: J201.7 (DAT0), R208.2, U201.98 (PC8)
SD_DAT1: J201.8 (DAT1), R207.2, U201.99 (PC9)
SD_DAT2: J201.1 (DAT2), R215.2, U201.111 (PC10)
SD_DAT3: J201.2 (DAT3/CD), R214.2, U201.112 (PC11)
SD_DETECT: C203.1, J201.10 (DET_A), R216.1, U201.103 (PA11)

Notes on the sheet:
SD Card
LCD / Display
JTAG Connector
EXP3 Connector
OSC
VDD3 (Pin 144)
USART1
USART2
SPI2
NSS
SCK
MISO
MOSI
SDIO
INT
JTAG
Analog
Level shifter
0 : SD inserted 1 : SD ejected

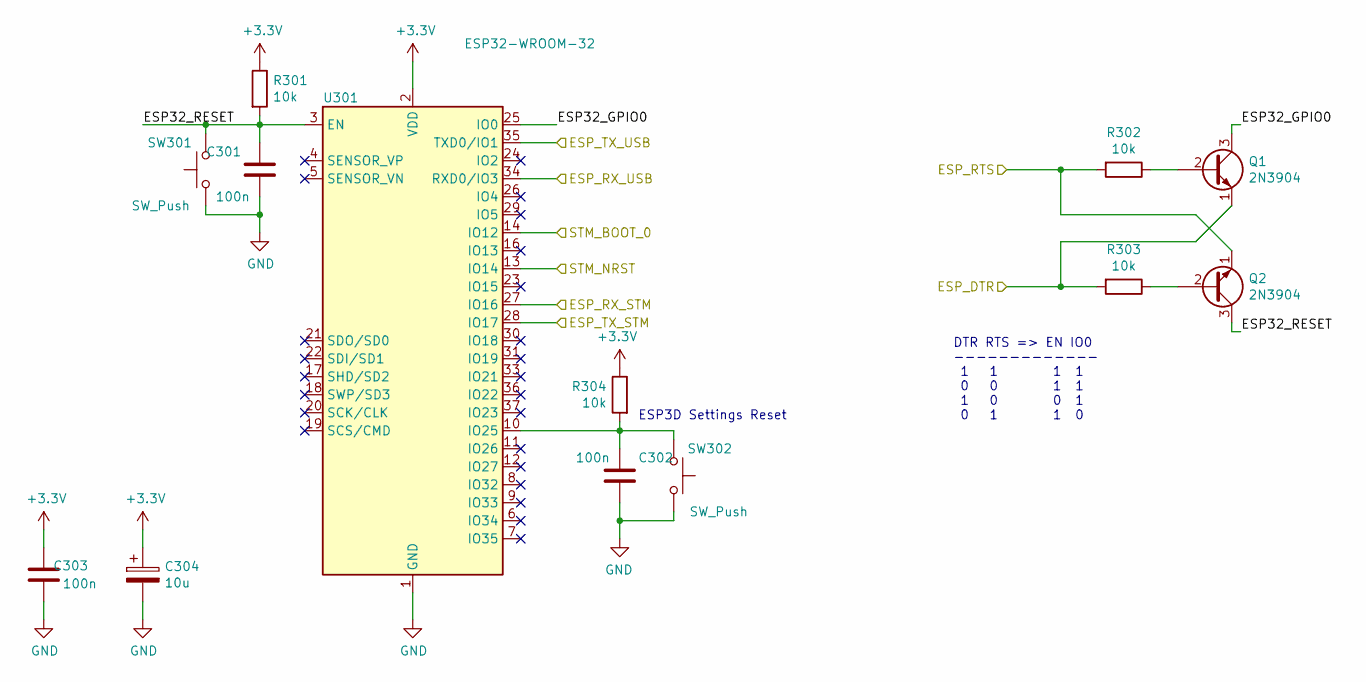
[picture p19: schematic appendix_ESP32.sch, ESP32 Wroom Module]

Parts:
C301, C302, C303: 100n; C_0603
C304: 10u; C_1210
Q1, Q2: 2N3904; SOT-23
R301, R302, R303, R304: 10k; R_0603
SW301, SW302: SW_Push; SW_SPST_KMR2
U301: ESP32-WROOM-32

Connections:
+3V3: C303.1, C304.1, R301.1, R304.1, U301.2 (VDD); also elsewhere on the board
/appendix_ESP32/ESP32_GPIO0: Q1.3 (C), U301.25 (IO0)
/appendix_ESP32/ESP32_RESET: C301.1, Q2.3 (C), R301.2, SW301.2, U301.3 (EN)
/appendix_ESP32/ESP_DTR: Q1.1 (E), R303.2; also elsewhere on the board
/appendix_ESP32/ESP_RTS: Q2.1 (E), R302.2; also elsewhere on the board
/appendix_ESP32/ESP_RX_STM: U301.27 (IO16); also elsewhere on the board
/appendix_ESP32/ESP_RX_USB: U301.34 (RXD0/IO3); also elsewhere on the board
/appendix_ESP32/ESP_TX_STM: U301.28 (IO17); also elsewhere on the board
/appendix_ESP32/ESP_TX_USB: U301.35 (TXD0/IO1); also elsewhere on the board
/appendix_STM32F103/STM32_BOOT_0: U301.14 (IO12); also elsewhere on the board
/appendix_STM32F103/STM32_NRST: U301.13 (IO14); also elsewhere on the board
GND: C301.2, C302.2, C303.2, C304.2, SW301.1, SW302.1, U301.1 (GND), U301.15 (GND), U301.38 (GND); also elsewhere on the board
unnamed: C302.1, R304.2, SW302.2, U301.10 (IO25)
unnamed: Q1.2 (B), R302.1
unnamed: Q2.2 (B), R303.1

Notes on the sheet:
ESP3D Settings Reset
DTR RTS => EN IO0 ------------- 1 1 1 1 0 0 1 1 1 0 0 1 0 1 1 0

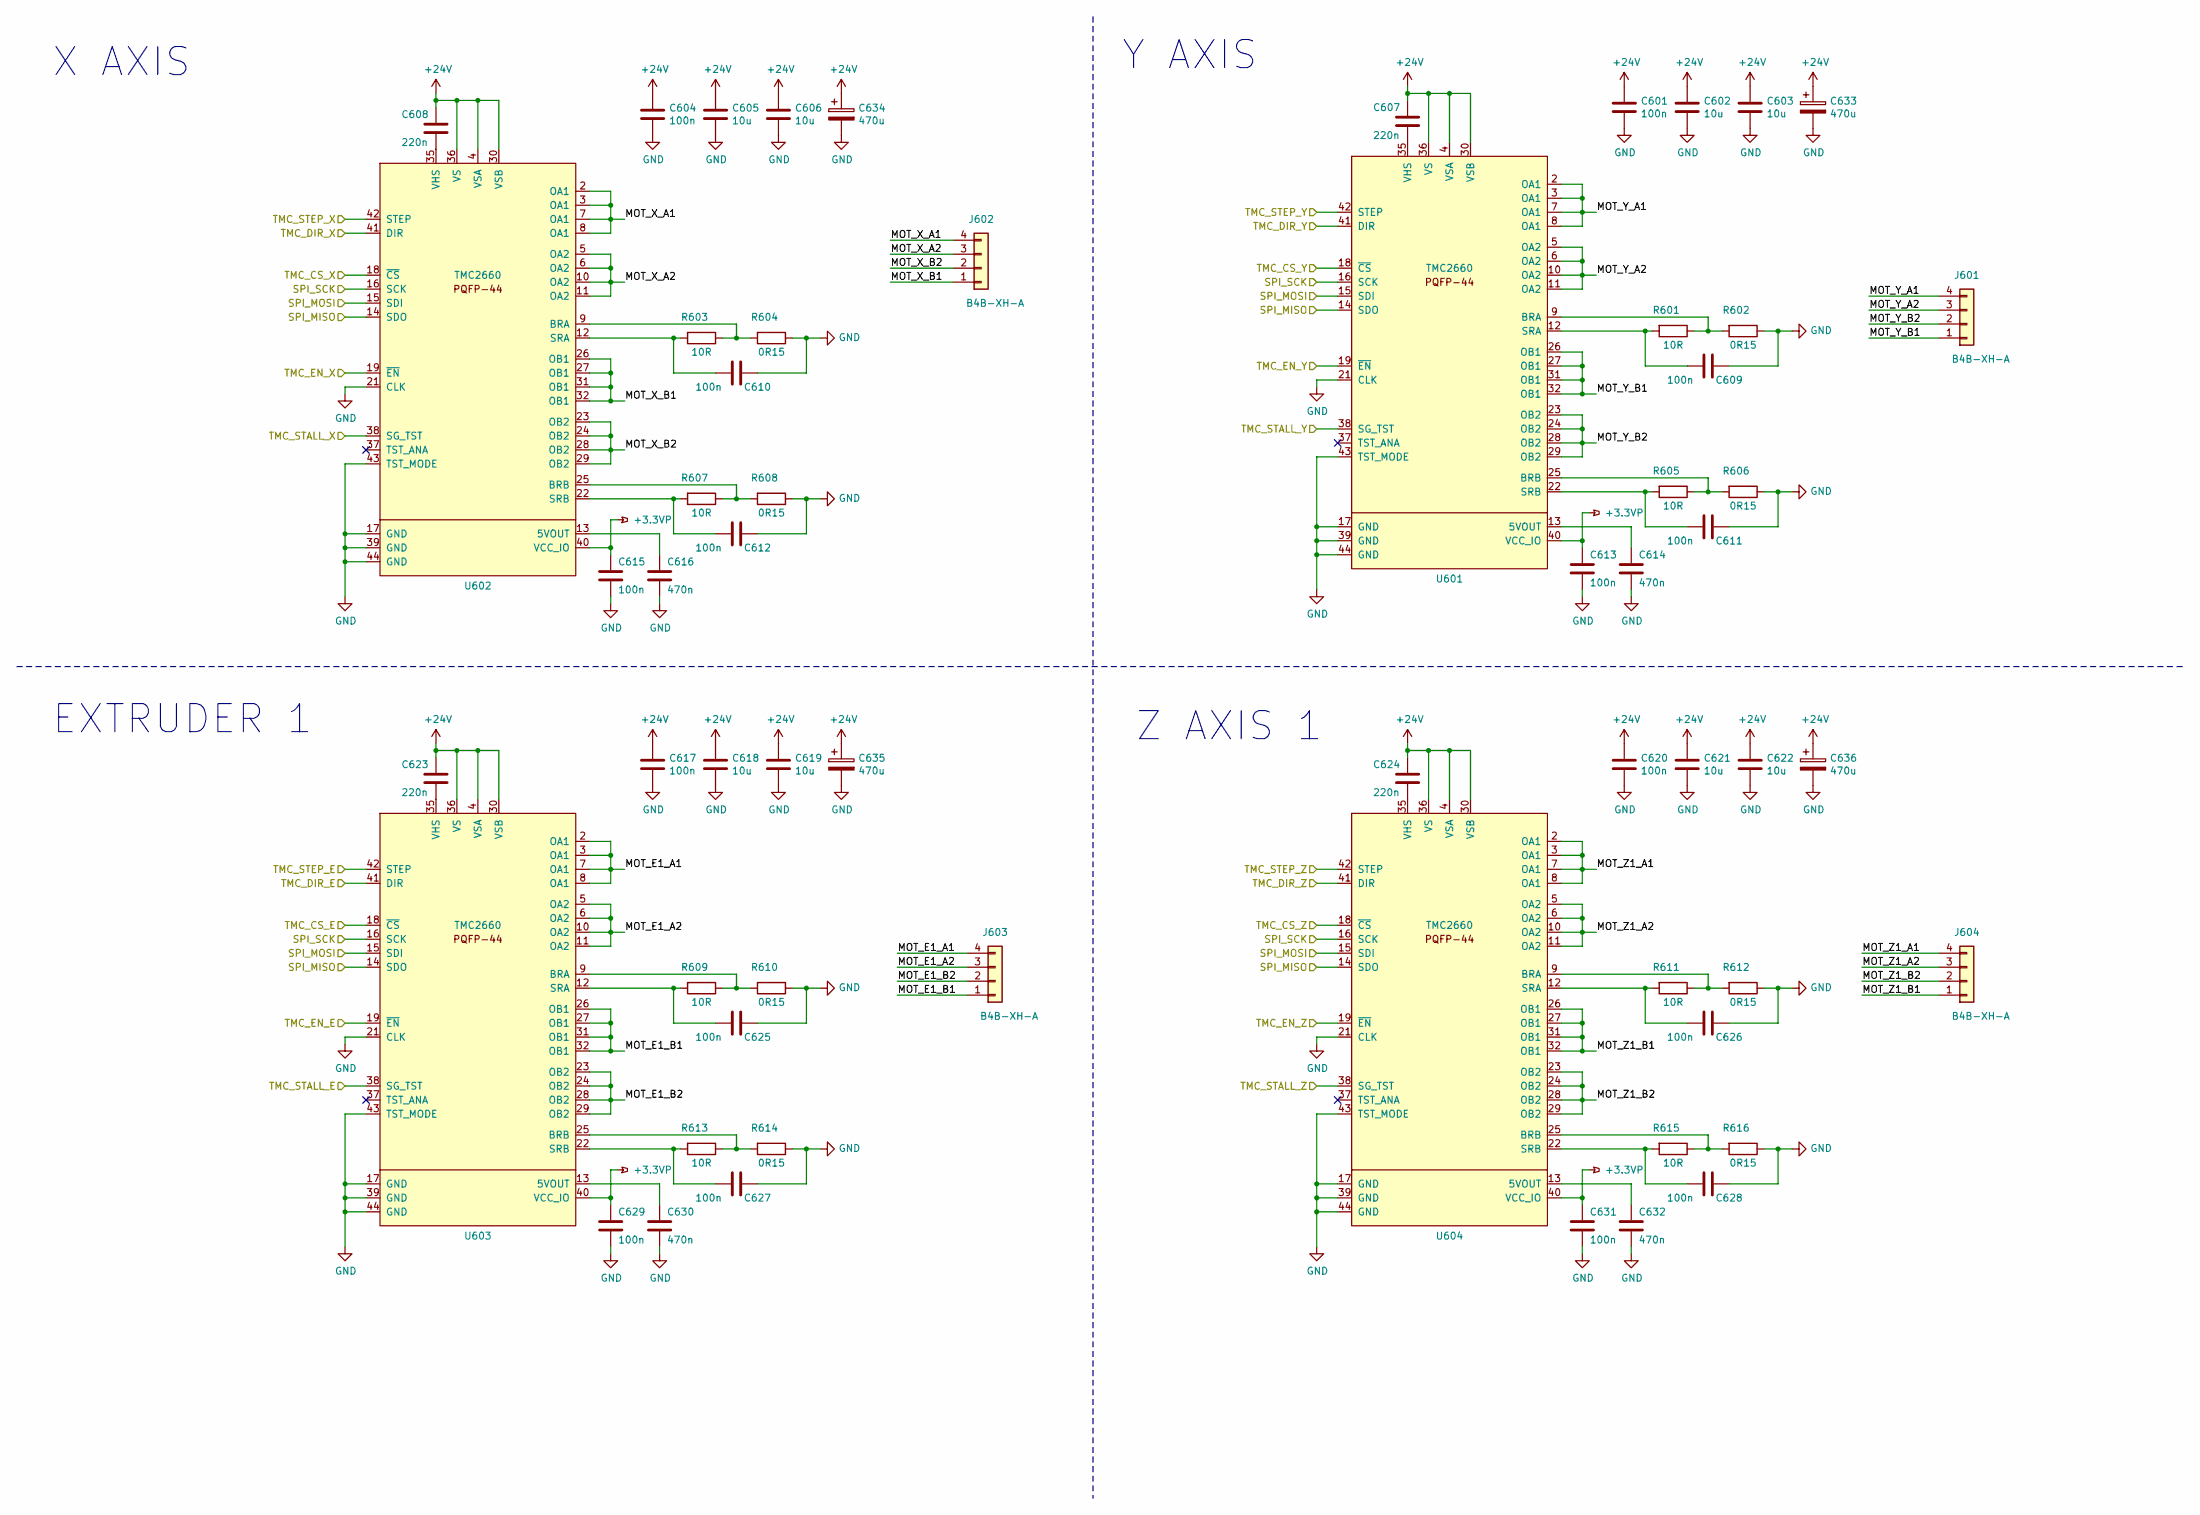
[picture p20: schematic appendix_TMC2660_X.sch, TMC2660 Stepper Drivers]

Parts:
C601, C604, C609, C610, C611, C612, C613, C615, C617, C620, C625, C626, C627, C628, C629, C631: 100n; C_0603
C602, C603, C605, C606, C618, C619, C621, C622: 10u; C_1210
C607, C608, C623, C624: 220n; C_0603
C614, C616, C630, C632: 470n; C_0603
C633, C634, C635, C636: 470u; CP_Elec_10x10
J601, J602, J603, J604: B4B-XH-A; JST_XH_B4B-XH-A_1x04_P2.50mm_Vertical
R601, R603, R605, R607, R609, R611, R613, R615: 10R; R_0603
R602, R604, R606, R608, R610, R612, R614, R616: 0R15; R_1210
U601, U602, U603, U604: TMC2660; TQFP-44_10x10mm

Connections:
+3.3VP: C613.1, C615.1, C629.1, C631.1, U601.40 (VCC_IO), U602.40 (VCC_IO), U603.40 (VCC_IO), U604.40 (VCC_IO); also elsewhere on the board
+24V: C601.1, C602.1, C603.1, C604.1, C605.1, C606.1, C607.1, C608.1, C617.1, C618.1, C619.1, C620.1, C621.1, C622.1, C623.1, C624.1, C633.1, C634.1, C635.1, C636.1, U601.4 (VSA), U601.30 (VSB), U601.36 (VS), U602.4 (VSA), U602.30 (VSB), U602.36 (VS), U603.4 (VSA), U603.30 (VSB), U603.36 (VS), U604.4 (VSA), U604.30 (VSB), U604.36 (VS); also elsewhere on the board
/appendix_STM32F103/CS_E1: U603.18 (~CS~); also elsewhere on the board
/appendix_STM32F103/CS_X: U602.18 (~CS~); also elsewhere on the board
/appendix_STM32F103/CS_Y: U601.18 (~CS~); also elsewhere on the board
/appendix_STM32F103/CS_Z1: U604.18 (~CS~); also elsewhere on the board
/appendix_STM32F103/DIR_E1: U603.41 (DIR); also elsewhere on the board
/appendix_STM32F103/DIR_X: U602.41 (DIR); also elsewhere on the board
/appendix_STM32F103/DIR_Y: U601.41 (DIR); also elsewhere on the board
/appendix_STM32F103/DIR_Z1: U604.41 (DIR); also elsewhere on the board
/appendix_STM32F103/EN_E1: U603.19 (~EN); also elsewhere on the board
/appendix_STM32F103/EN_X: U602.19 (~EN); also elsewhere on the board
/appendix_STM32F103/EN_Y: U601.19 (~EN); also elsewhere on the board
/appendix_STM32F103/EN_Z1: U604.19 (~EN); also elsewhere on the board
/appendix_STM32F103/STALL_E1: U603.38 (SG_TST); also elsewhere on the board
/appendix_STM32F103/STALL_X: U602.38 (SG_TST); also elsewhere on the board
/appendix_STM32F103/STALL_Y: U601.38 (SG_TST); also elsewhere on the board
/appendix_STM32F103/STALL_Z1: U604.38 (SG_TST); also elsewhere on the board
/appendix_STM32F103/STEP_E1: U603.42 (STEP); also elsewhere on the board
/appendix_STM32F103/STEP_X: U602.42 (STEP); also elsewhere on the board
/appendix_STM32F103/STEP_Y: U601.42 (STEP); also elsewhere on the board
/appendix_STM32F103/STEP_Z1: U604.42 (STEP); also elsewhere on the board
/appendix_TMC2660_X/MOT_E1_A1: J603.4, U603.2 (OA1), U603.3 (OA1), U603.7 (OA1), U603.8 (OA1)
/appendix_TMC2660_X/MOT_E1_A2: J603.3, U603.5 (OA2), U603.6 (OA2), U603.10 (OA2), U603.11 (OA2)
/appendix_TMC2660_X/MOT_E1_B1: J603.1, U603.26 (OB1), U603.27 (OB1), U603.31 (OB1), U603.32 (OB1)
/appendix_TMC2660_X/MOT_E1_B2: J603.2, U603.23 (OB2), U603.24 (OB2), U603.28 (OB2), U603.29 (OB2)
/appendix_TMC2660_X/MOT_X_A1: J602.4, U602.2 (OA1), U602.3 (OA1), U602.7 (OA1), U602.8 (OA1)
/appendix_TMC2660_X/MOT_X_A2: J602.3, U602.5 (OA2), U602.6 (OA2), U602.10 (OA2), U602.11 (OA2)
/appendix_TMC2660_X/MOT_X_B1: J602.1, U602.26 (OB1), U602.27 (OB1), U602.31 (OB1), U602.32 (OB1)
/appendix_TMC2660_X/MOT_X_B2: J602.2, U602.23 (OB2), U602.24 (OB2), U602.28 (OB2), U602.29 (OB2)
/appendix_TMC2660_X/MOT_Y_A1: J601.4, U601.2 (OA1), U601.3 (OA1), U601.7 (OA1), U601.8 (OA1)
/appendix_TMC2660_X/MOT_Y_A2: J601.3, U601.5 (OA2), U601.6 (OA2), U601.10 (OA2), U601.11 (OA2)
/appendix_TMC2660_X/MOT_Y_B1: J601.1, U601.26 (OB1), U601.27 (OB1), U601.31 (OB1), U601.32 (OB1)
/appendix_TMC2660_X/MOT_Y_B2: J601.2, U601.23 (OB2), U601.24 (OB2), U601.28 (OB2), U601.29 (OB2)
/appendix_TMC2660_X/MOT_Z1_A1: J604.4, U604.2 (OA1), U604.3 (OA1), U604.7 (OA1), U604.8 (OA1)
/appendix_TMC2660_X/MOT_Z1_A2: J604.3, U604.5 (OA2), U604.6 (OA2), U604.10 (OA2), U604.11 (OA2)
/appendix_TMC2660_X/MOT_Z1_B1: J604.1, U604.26 (OB1), U604.27 (OB1), U604.31 (OB1), U604.32 (OB1)
/appendix_TMC2660_X/MOT_Z1_B2: J604.2, U604.23 (OB2), U604.24 (OB2), U604.28 (OB2), U604.29 (OB2)
GND: C601.2, C602.2, C603.2, C604.2, C605.2, C606.2, C609.1, C610.1, C611.1, C612.1, C613.2, C614.2, C615.2, C616.2, C617.2, C618.2, C619.2, C620.2, C621.2, C622.2, C625.1, C626.1, C627.1, C628.1, C629.2, C630.2, C631.2, C632.2, C633.2, C634.2, C635.2, C636.2, R602.1, R604.1, R606.1, R608.1, R610.1, R612.1, R614.1, R616.1, U601.17 (GND), U601.21 (CLK), U601.39 (GND), U601.43 (TST_MODE), U601.44 (GND), U602.17 (GND), U602.21 (CLK), U602.39 (GND), U602.43 (TST_MODE), U602.44 (GND), U603.17 (GND), U603.21 (CLK), U603.39 (GND), U603.43 (TST_MODE), U603.44 (GND), U604.17 (GND), U604.21 (CLK), U604.39 (GND), U604.43 (TST_MODE), U604.44 (GND); also elsewhere on the board
MISO: U601.14 (SDO), U602.14 (SDO), U603.14 (SDO), U604.14 (SDO); also elsewhere on the board
MOSI: U601.15 (SDI), U602.15 (SDI), U603.15 (SDI), U604.15 (SDI); also elsewhere on the board
unnamed: C607.2, U601.35 (VHS)
unnamed: C608.2, U602.35 (VHS)
unnamed: C609.2, R601.2, U601.12 (SRA)
unnamed: C610.2, R603.2, U602.12 (SRA)
unnamed: C611.2, R605.2, U601.22 (SRB)
unnamed: C612.2, R607.2, U602.22 (SRB)
unnamed: C614.1, U601.13 (5VOUT)
unnamed: C616.1, U602.13 (5VOUT)
unnamed: C623.2, U603.35 (VHS)
unnamed: C624.2, U604.35 (VHS)
unnamed: C625.2, R609.2, U603.12 (SRA)
unnamed: C626.2, R611.2, U604.12 (SRA)
unnamed: C627.2, R613.2, U603.22 (SRB)
unnamed: C628.2, R615.2, U604.22 (SRB)
unnamed: C630.1, U603.13 (5VOUT)
unnamed: C632.1, U604.13 (5VOUT)
unnamed: R601.1, R602.2, U601.9 (BRA)
unnamed: R603.1, R604.2, U602.9 (BRA)
unnamed: R605.1, R606.2, U601.25 (BRB)
unnamed: R607.1, R608.2, U602.25 (BRB)
unnamed: R609.1, R610.2, U603.9 (BRA)
unnamed: R611.1, R612.2, U604.9 (BRA)
unnamed: R613.1, R614.2, U603.25 (BRB)
unnamed: R615.1, R616.2, U604.25 (BRB)
SCK: U601.16 (SCK), U602.16 (SCK), U603.16 (SCK), U604.16 (SCK); also elsewhere on the board

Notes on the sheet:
X AXIS
EXTRUDER 1
Z AXIS 1
Y AXIS

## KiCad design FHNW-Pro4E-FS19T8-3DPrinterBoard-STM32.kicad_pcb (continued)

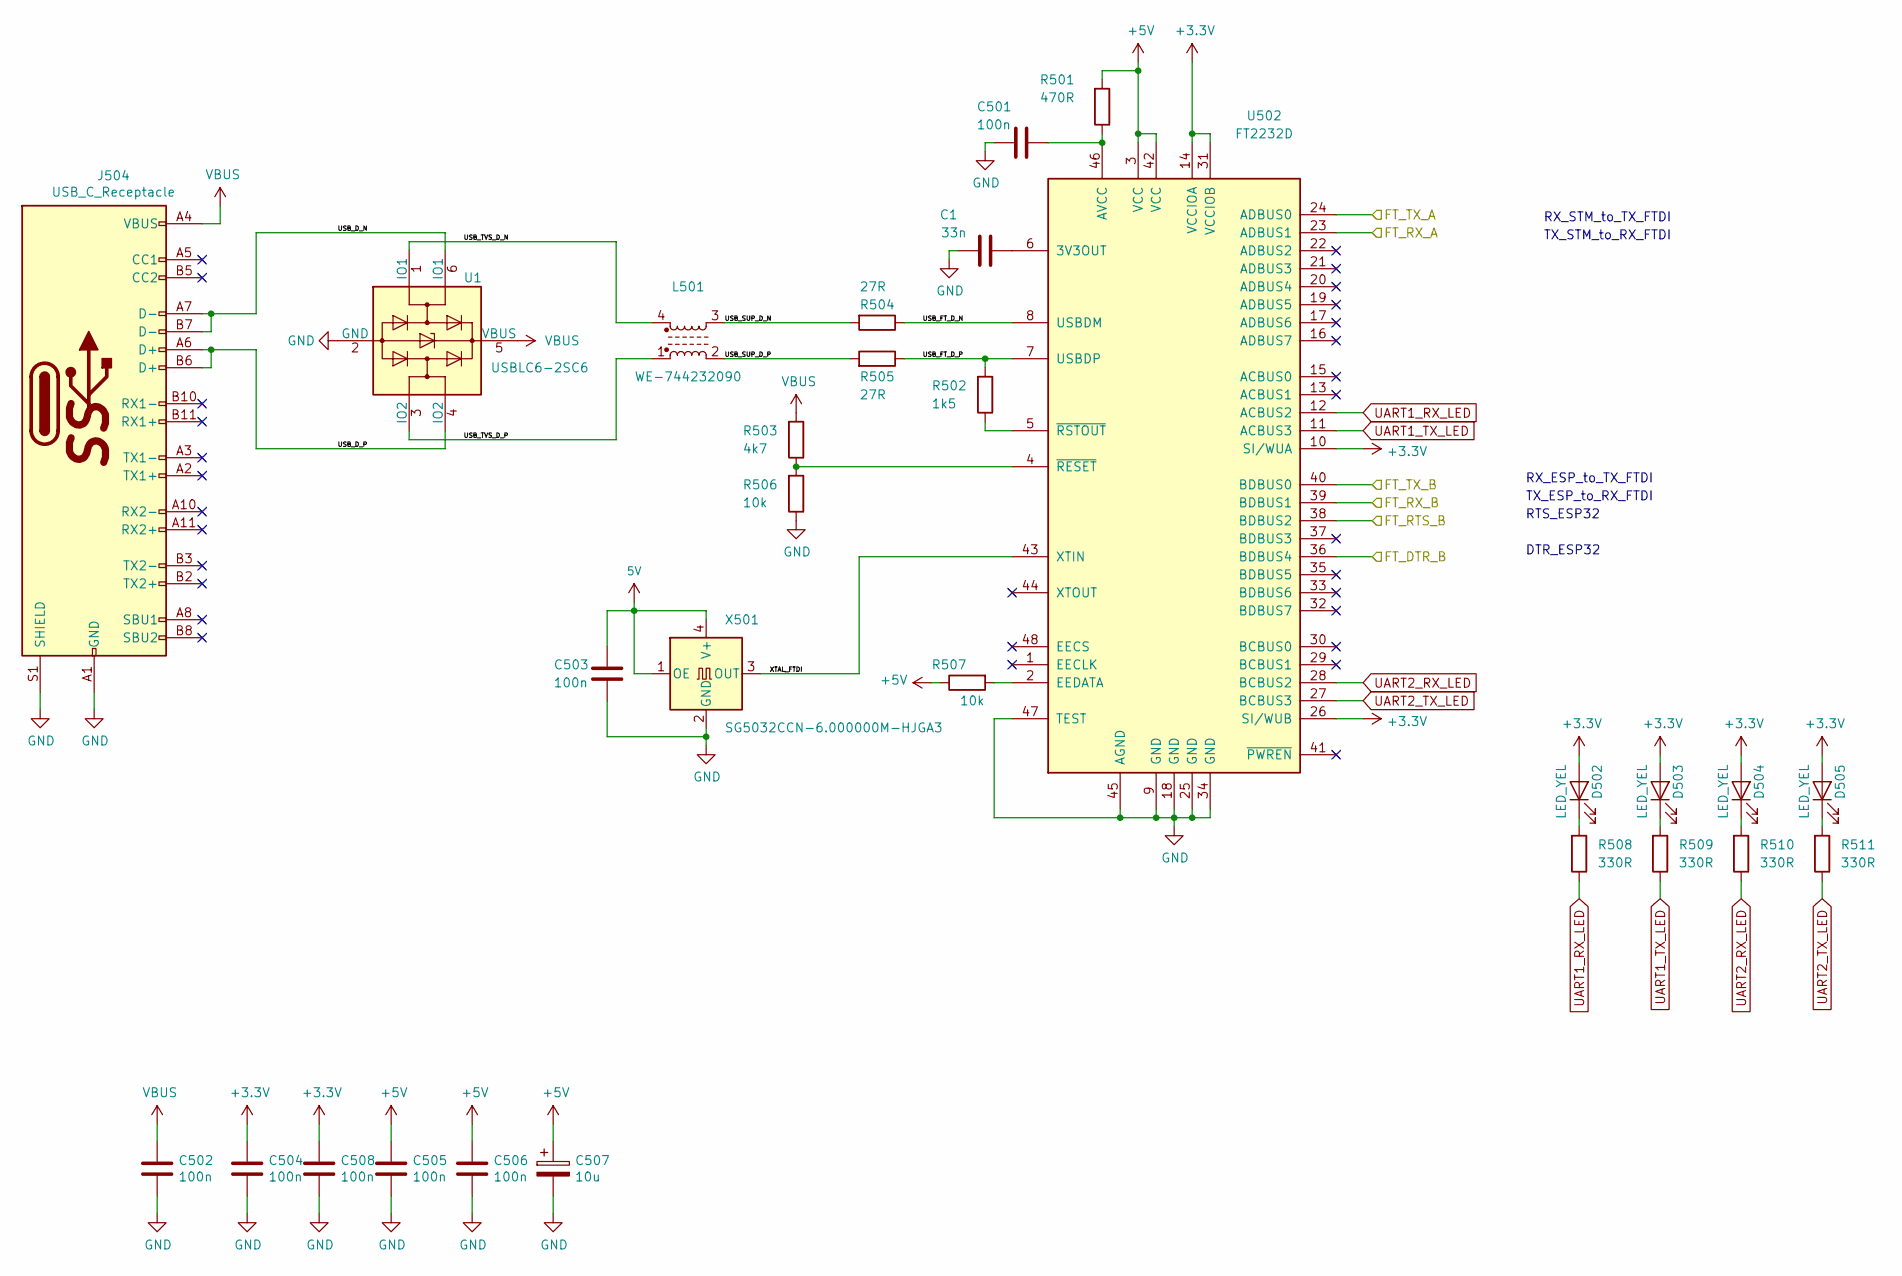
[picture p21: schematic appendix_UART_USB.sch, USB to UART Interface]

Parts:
C1: 33n; C_0603
C501, C502, C503, C504, C505, C506, C508: 100n; C_0603
C507: 10u; C_1210
D502, D503, D504, D505: LED_YEL; LED_0805_2012Metric
J504: USB_C_Receptacle; USB_C_Receptacle_Amphenol_12401610E4-2A
L501: WE-744232090; WURTH_USB_Chocke_4PAD
R501: 470R; R_0603
R502: 1k5; R_0603
R503: 4k7; R_0603
R504, R505: 27R; R_0603
R506, R507: 10k; R_0603
R508, R509, R510, R511: 330R; R_0603
U1: USBLC6-2SC6; SOT-23-6
U502: FT2232D; LQFP-48_7x7mm_P0.5mm
X501: SG5032CCN-6.000000M-HJGA3; Oscillator_SMD_SeikoEpson_SG8002LB-4Pin_5.0x3.2mm

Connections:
+3V3: C504.1, C508.1, D502.2 (A), D503.2 (A), D504.2 (A), D505.2 (A), U502.10 (SI/WUA), U502.14 (VCCIOA), U502.26 (SI/WUB), U502.31 (VCCIOB); also elsewhere on the board
/appendix_ESP32/ESP_DTR: U502.36 (BDBUS4); also elsewhere on the board
/appendix_ESP32/ESP_RTS: U502.38 (BDBUS2); also elsewhere on the board
/appendix_ESP32/ESP_RX_USB: U502.40 (BDBUS0); also elsewhere on the board
/appendix_ESP32/ESP_TX_USB: U502.39 (BDBUS1); also elsewhere on the board
/appendix_UART_USB/FT_RX_A: U502.23 (ADBUS1); also elsewhere on the board
/appendix_UART_USB/FT_TX_A: U502.24 (ADBUS0); also elsewhere on the board
/appendix_UART_USB/USB_D_N: J504.A7 (D-), J504.B7 (D-), U1.6 (IO1)
/appendix_UART_USB/USB_D_P: J504.A6 (D+), J504.B6 (D+), U1.4 (IO2)
/appendix_UART_USB/USB_FT_D_N: R504.1, U502.8 (USBDM)
/appendix_UART_USB/USB_FT_D_P: R502.2, R505.1, U502.7 (USBDP)
/appendix_UART_USB/USB_SUP_D_N: L501.3, R504.2
/appendix_UART_USB/USB_SUP_D_P: L501.2, R505.2
/appendix_UART_USB/USB_TVS_D_N: L501.4, U1.1 (IO1)
/appendix_UART_USB/USB_TVS_D_P: L501.1, U1.3 (IO2)
/appendix_UART_USB/XTAL_FTDI: U502.43 (XTIN), X501.3 (OUT)
GND: C1.1, C501.2, C502.2, C503.2, C504.2, C505.2, C506.2, C507.2, C508.2, J504.A1 (GND), J504.A12 (GND), J504.B1 (GND), J504.B12 (GND), J504.S1 (SHIELD), R506.1, U1.2 (GND), U502.9 (GND), U502.18 (GND), U502.25 (GND), U502.34 (GND), U502.45 (AGND), U502.47 (TEST), X501.2 (GND); also elsewhere on the board
unnamed: C1.2, U502.6 (3V3OUT)
unnamed: C501.1, R501.1, U502.46 (AVCC)
unnamed: D502.1 (K), R508.2
unnamed: D503.1 (K), R509.2
unnamed: D504.1 (K), R510.2
unnamed: D505.1 (K), R511.2
unnamed: R502.1, U502.5 (~RSTOUT)
unnamed: R503.1, R506.2, U502.4 (~RESET)
unnamed: R507.2, U502.2 (EEDATA)
UART1_RX_LED: R508.1, U502.12 (ACBUS2)
UART1_TX_LED: R509.1, U502.11 (ACBUS3)
UART2_RX_LED: R510.1, U502.28 (BCBUS2)
UART2_TX_LED: R511.1, U502.27 (BCBUS3)
VBUS: C502.1, J504.A4 (VBUS), J504.A9 (VBUS), J504.B4 (VBUS), J504.B9 (VBUS), R503.2, U1.5 (VBUS)

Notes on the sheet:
RX_STM_to_TX_FTDI
TX_STM_to_RX_FTDI
RX_ESP_to_TX_FTDI
TX_ESP_to_RX_FTDI
RTS_ESP32
DTR_ESP32

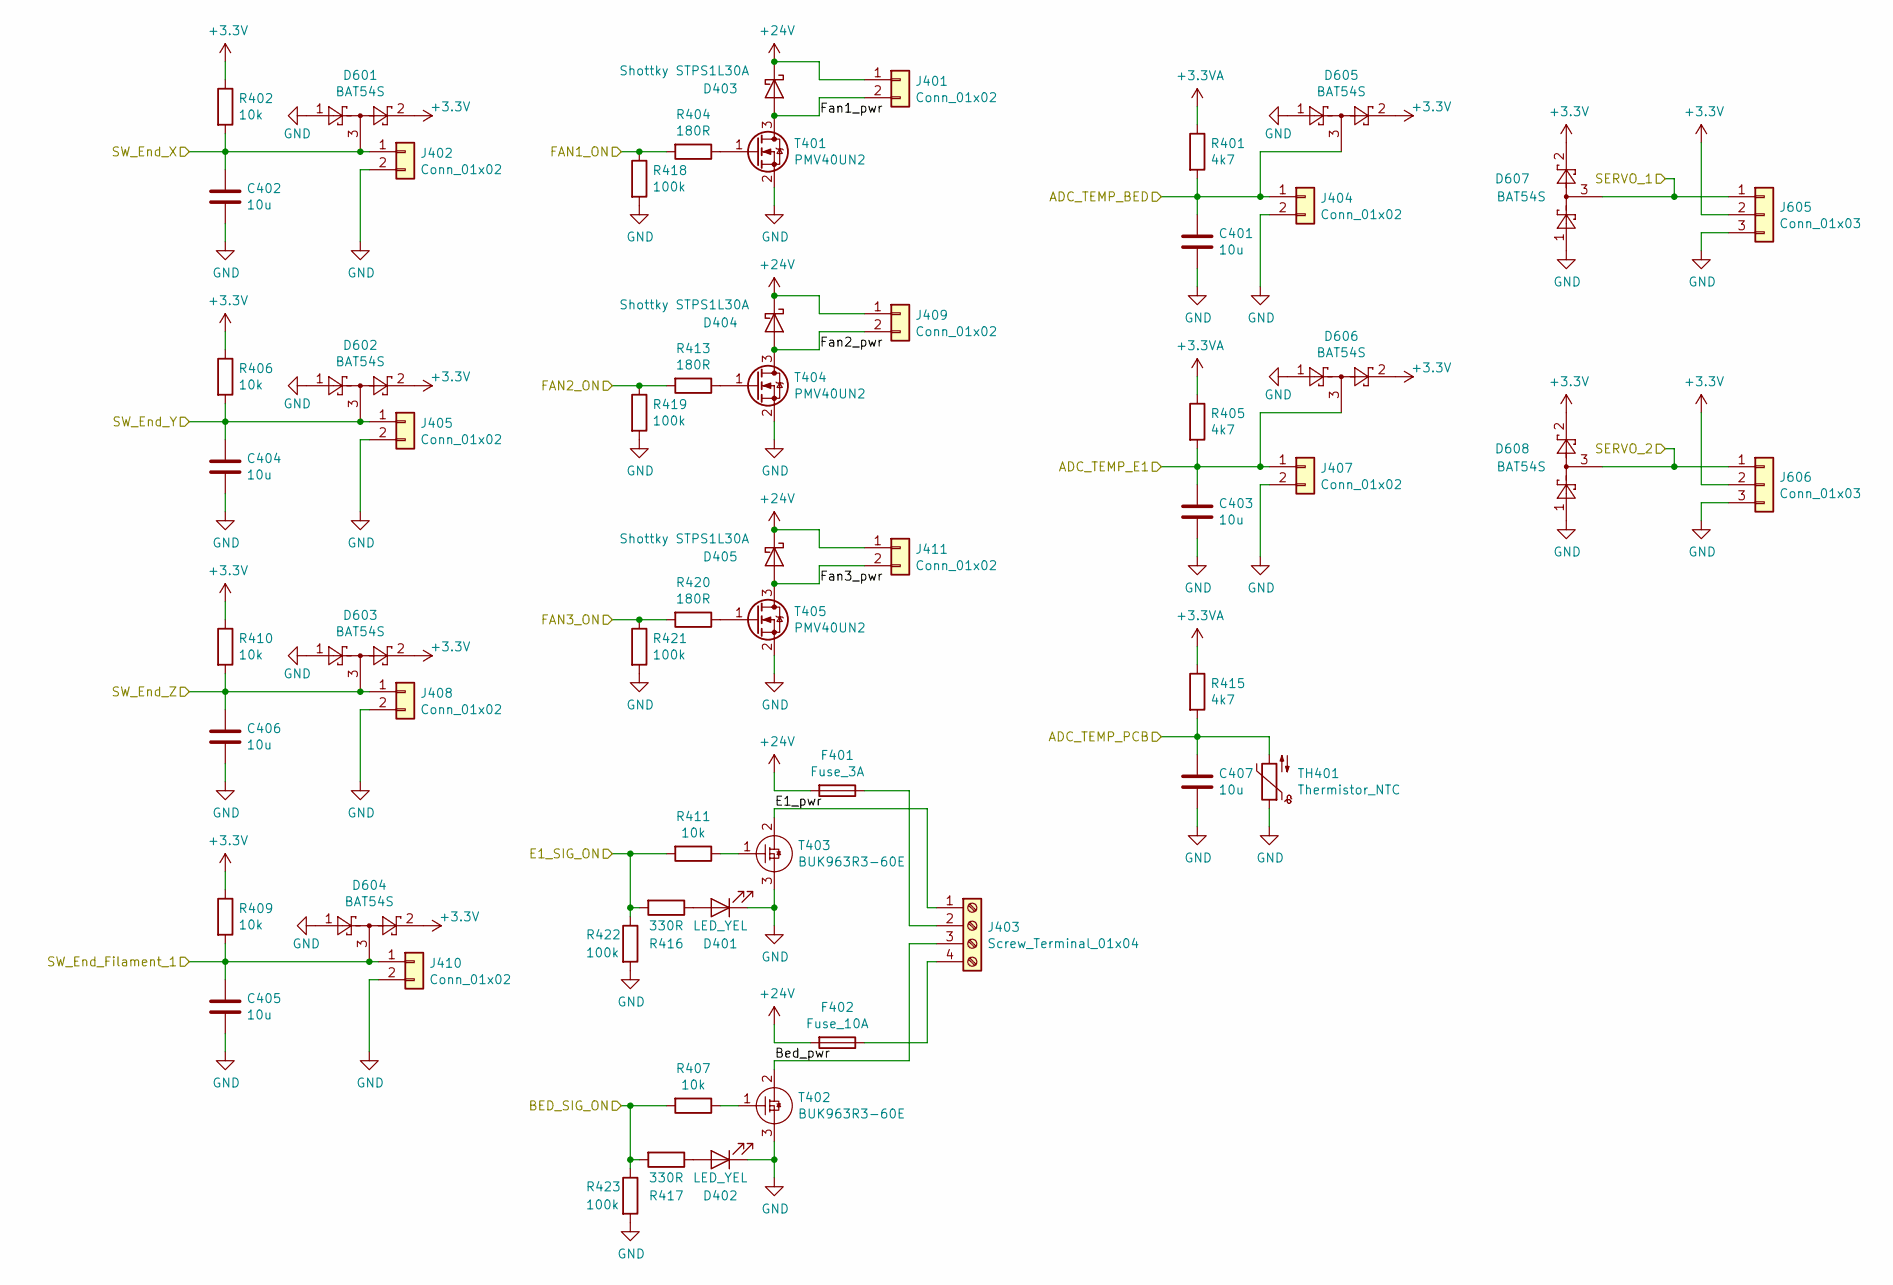
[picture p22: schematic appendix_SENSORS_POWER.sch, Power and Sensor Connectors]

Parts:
C401, C402, C403, C404, C405, C406, C407: 10u; C_1210
D401, D402: LED_YEL; LED_0805_2012Metric
D403, D404, D405: Shottky STPS1L30A; D_SMB
D601, D602, D603, D604, D605, D606, D607, D608: BAT54S; SOT-23
F401: Fuse_3A; Fuseholder_Blade_ATO_Littelfuse_Pudenz_2_Pin
F402: Fuse_10A; Fuseholder_Blade_ATO_Littelfuse_Pudenz_2_Pin
J401, J402, J404, J405, J407, J408, J409, J410, J411: Conn_01x02; JST_EH_B02B-EH-A_02x2.50mm_Straight
J403: Screw_Terminal_01x04; TerminalBlock_Altech_AK300-4_P5.00mm
J605, J606: Conn_01x03; PinHeader_1x03_P2.54mm_Vertical
R401, R405, R415: 4k7; R_0603
R402, R406, R407, R409, R410, R411: 10k; R_0603
R404, R413, R420: 180R; R_0603
R416, R417: 330R; R_0603
R418, R419, R421, R422, R423: 100k; R_0603
T401, T404, T405: PMV40UN2; SOT-23
T402, T403: BUK963R3-60E; TO-263-2
TH401: Thermistor_NTC; R_0805_HandSoldering

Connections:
+3.3VA: R401.1, R405.1, R415.1; also elsewhere on the board
+3V3: D601.2, D602.2, D603.2, D604.2, D605.2, D606.2, D607.2, D608.2, J605.2, J606.2, R402.1, R406.1, R409.1, R410.1; also elsewhere on the board
+24V: D403.1 (K), D404.1 (K), D405.1 (K), F401.2, F402.2, J401.1, J409.1, J411.1; also elsewhere on the board
/appendix_SENSORS_POWER/ADC_TEMP_BED: C401.1, D605.3, J404.1, R401.2; also elsewhere on the board
/appendix_SENSORS_POWER/ADC_TEMP_E1: C403.1, D606.3, J407.1, R405.2; also elsewhere on the board
/appendix_SENSORS_POWER/ADC_TEMP_PCB: C407.1, R415.2, TH401.2; also elsewhere on the board
/appendix_SENSORS_POWER/Bed_pwr: J403.3, T402.2
/appendix_SENSORS_POWER/E1_pwr: J403.1, T403.2
/appendix_SENSORS_POWER/Fan1_pwr: D403.2 (A), J401.2, T401.3 (D)
/appendix_SENSORS_POWER/Fan2_pwr: D404.2 (A), J409.2, T404.3 (D)
/appendix_SENSORS_POWER/Fan3_pwr: D405.2 (A), J411.2, T405.3 (D)
/appendix_SENSORS_POWER/SERVO_1: D607.3, J605.1; also elsewhere on the board
/appendix_SENSORS_POWER/SERVO_2: D608.3, J606.1; also elsewhere on the board
/appendix_SENSORS_POWER/SW_End_Filament_1: C405.1, D604.3, J410.1, R409.2; also elsewhere on the board
/appendix_SENSORS_POWER/SW_End_X: C402.1, D601.3, J402.1, R402.2; also elsewhere on the board
/appendix_SENSORS_POWER/SW_End_Y: C404.1, D602.3, J405.1, R406.2; also elsewhere on the board
/appendix_SENSORS_POWER/SW_End_Z: C406.1, D603.3, J408.1, R410.2; also elsewhere on the board
/appendix_STM32F103/BED_ON: R407.2, R417.2, R423.1; also elsewhere on the board
/appendix_STM32F103/E1_ON: R411.2, R416.2, R422.1; also elsewhere on the board
/appendix_STM32F103/FAN1: R404.2, R418.1; also elsewhere on the board
/appendix_STM32F103/FAN2: R413.2, R419.1; also elsewhere on the board
/appendix_STM32F103/FAN3: R420.2, R421.1; also elsewhere on the board
GND: C401.2, C402.2, C403.2, C404.2, C405.2, C406.2, C407.2, D401.1 (K), D402.1 (K), D601.1, D602.1, D603.1, D604.1, D605.1, D606.1, D607.1, D608.1, J402.2, J404.2, J405.2, J407.2, J408.2, J410.2, J605.3, J606.3, R418.2, R419.2, R421.2, R422.2, R423.2, T401.2 (S), T402.3, T403.3, T404.2 (S), T405.2 (S), TH401.1; also elsewhere on the board
unnamed: D401.2 (A), R416.1
unnamed: D402.2 (A), R417.1
unnamed: F401.1, J403.2
unnamed: F402.1, J403.4
unnamed: R404.1, T401.1 (G)
unnamed: R407.1, T402.1
unnamed: R411.1, T403.1
unnamed: R413.1, T404.1 (G)
unnamed: R420.1, T405.1 (G)

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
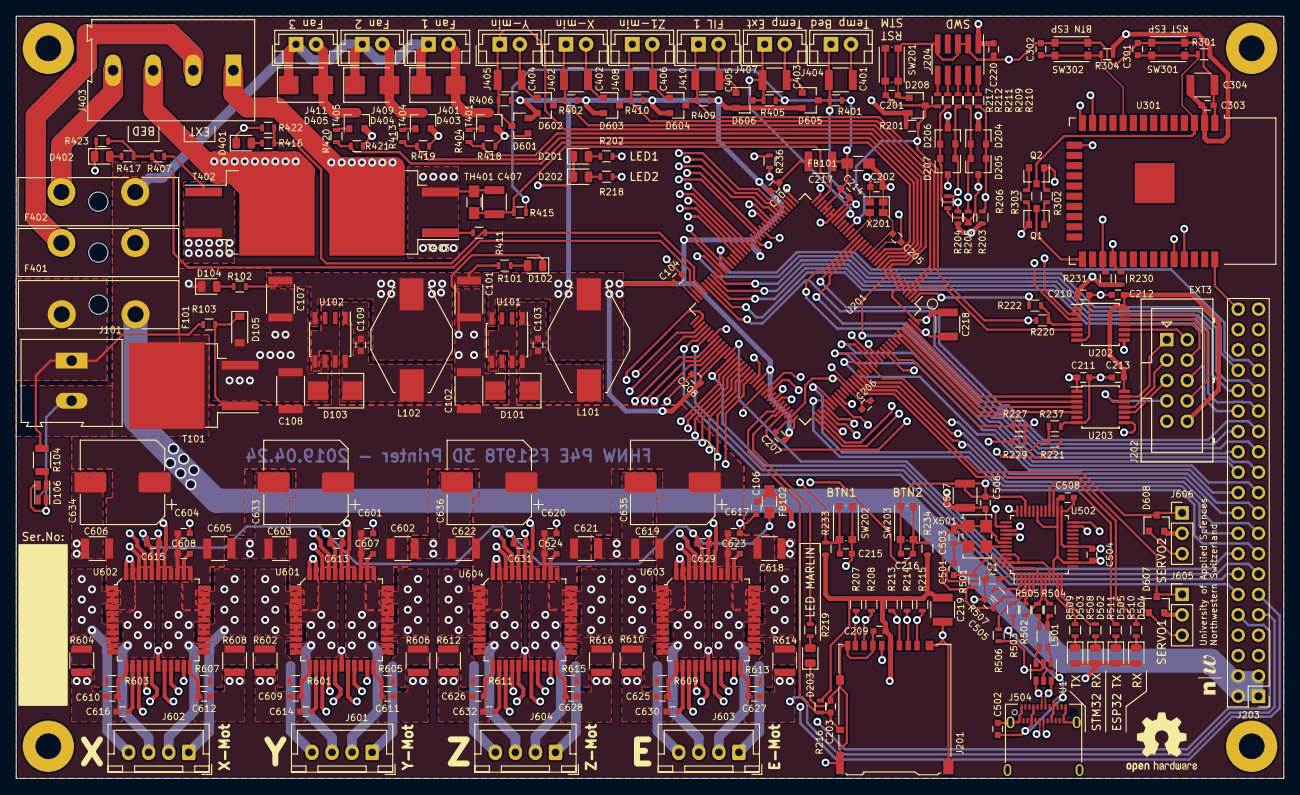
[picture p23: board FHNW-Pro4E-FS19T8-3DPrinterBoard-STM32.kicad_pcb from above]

Board: 4 copper layers, 158.0 x 95.0 mm, 264 parts (0 on the bottom side), 212 nets.

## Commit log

2019-04-02 created hierarchical .sch files added library with TMC2660 and BUK963 copied schematics for TMC2660 and various sensors/power in/out
    [FHNW-Pro4E-FS19T8-3DPrinterBoard-STM32.kicad_pcb, FHNW-Pro4E-FS19T8-3DPrinterBoard-STM32.sch, appendix_ESP32.sch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]
2019-04-03 added FTDI chip
    [FHNW-Pro4E-FS19T8-3DPrinterBoard-STM32.sch, appendix_ESP32.sch, appendix_POWER_PSU.sch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]
2019-04-03 merged hierarchical schematics
    [FHNW-Pro4E-FS19T8-3DPrinterBoard-STM32.sch, appendix_ESP32.sch, appendix_POWER_PSU.sch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]
2019-04-09 pre Annotation 1
    [FHNW-Pro4E-FS19T8-3DPrinterBoard-STM32.sch, appendix_ESP32.sch, appendix_SENSORS_POWER.sch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]
2019-04-09 1st annotation, footprints, netlist
    [FHNW-Pro4E-FS19T8-3DPrinterBoard-STM32.kicad_pcb, FHNW-Pro4E-FS19T8-3DPrinterBoard-STM32.sch, appendix_ESP32.sch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]
2019-04-09 started layouting TMC2660
    [FHNW-Pro4E-FS19T8-3DPrinterBoard-STM32.kicad_pcb, FHNW-Pro4E-FS19T8-3DPrinterBoard-STM32.sch, appendix_ESP32.sch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]
2019-04-12 Layout: all TMC / Schematic: Oli's comments
    [FHNW-Pro4E-FS19T8-3DPrinterBoard-STM32.kicad_pcb, FHNW-Pro4E-FS19T8-3DPrinterBoard-STM32.sch, appendix_ESP32.sch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]
2019-04-12 Printed Schematic for review process
2019-04-13 added footprints, layouted 3v3 Reg
    [FHNW-Pro4E-FS19T8-3DPrinterBoard-STM32.kicad_pcb, FHNW-Pro4E-FS19T8-3DPrinterBoard-STM32.sch, appendix_ESP32.sch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]
2019-04-13 added LEDs
    [FHNW-Pro4E-FS19T8-3DPrinterBoard-STM32.kicad_pcb, FHNW-Pro4E-FS19T8-3DPrinterBoard-STM32.sch, appendix_SENSORS_POWER.sch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]
2019-04-16 corrected P.S. Schematic review
    [FHNW-Pro4E-FS19T8-3DPrinterBoard-STM32.kicad_pcb, FHNW-Pro4E-FS19T8-3DPrinterBoard-STM32.sch, appendix_SENSORS_POWER.sch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]
2019-04-19 added FT2232 by Marco M
    [FHNW-Pro4E-FS19T8-3DPrinterBoard-STM32.kicad_pcb, appendix_ESP32.sch, appendix_SENSORS_POWER.sch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]
2019-04-21 fixed missing symbol issue fixed 3vout cap on FTDI
    [FHNW-Pro4E-FS19T8-3DPrinterBoard-STM32.sch, appendix_ESP32.sch, appendix_STM32F103.sch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]
2019-04-22 started with STM32 Pinout connections (Mittagspause)
    [FHNW-Pro4E-FS19T8-3DPrinterBoard-STM32.kicad_pcb, FHNW-Pro4E-FS19T8-3DPrinterBoard-STM32.sch, appendix_ESP32.sch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]
2019-04-22 layouted FT2232 / SD card
    [FHNW-Pro4E-FS19T8-3DPrinterBoard-STM32.kicad_pcb, appendix_STM32F103.sch, appendix_UART_USB.sch]
2019-04-22 added cache.lib to git
    [FHNW-Pro4E-FS19T8-3DPrinterBoard-STM32.kicad_pcb, FHNW-Pro4E-FS19T8-3DPrinterBoard-STM32.sch, appendix_STM32F103.sch]
2019-04-22 cleaned up Layout
    [FHNW-Pro4E-FS19T8-3DPrinterBoard-STM32.kicad_pcb, appendix_SENSORS_POWER.sch, appendix_STM32F103.sch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]
2019-04-23 Layout update
    [FHNW-Pro4E-FS19T8-3DPrinterBoard-STM32.kicad_pcb, FHNW-Pro4E-FS19T8-3DPrinterBoard-STM32.sch, appendix_STM32F103.sch]
2019-04-23 having issues with netclasses
    [FHNW-Pro4E-FS19T8-3DPrinterBoard-STM32.kicad_pcb, FHNW-Pro4E-FS19T8-3DPrinterBoard-STM32.sch, appendix_ESP32.sch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]
2019-04-23 Layoutet Power 3.3V / 5V
    [FHNW-Pro4E-FS19T8-3DPrinterBoard-STM32.kicad_pcb]
2019-04-23 first layout draft without 40pin
    [FHNW-Pro4E-FS19T8-3DPrinterBoard-STM32.kicad_pcb, FHNW-Pro4E-FS19T8-3DPrinterBoard-STM32.sch, appendix_STM32F103.sch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]
2019-04-24 user LED + fixes in Layout
    [FHNW-Pro4E-FS19T8-3DPrinterBoard-STM32.kicad_pcb, FHNW-Pro4E-FS19T8-3DPrinterBoard-STM32.sch, appendix_STM32F103.sch]
2019-04-24 TVS protection, BOOT1 pin, user BTN
    [FHNW-Pro4E-FS19T8-3DPrinterBoard-STM32.kicad_pcb, FHNW-Pro4E-FS19T8-3DPrinterBoard-STM32.sch, appendix_ESP32.sch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]
2019-04-24 finished up for final review
    [FHNW-Pro4E-FS19T8-3DPrinterBoard-STM32-B_Cu.gbr, FHNW-Pro4E-FS19T8-3DPrinterBoard-STM32-B_Mask.gbr, FHNW-Pro4E-FS19T8-3DPrinterBoard-STM32-B_Paste.gbr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]
2019-04-24 fixed minor layout stuff with mueller
    [FHNW-Pro4E-FS19T8-3DPrinterBoard-STM32-B_Cu.gbr, FHNW-Pro4E-FS19T8-3DPrinterBoard-STM32-B_Mask.gbr, FHNW-Pro4E-FS19T8-3DPrinterBoard-STM32-B_Paste.gbr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]
2019-04-25 changed screw terminal for bed/ext
    [FHNW-Pro4E-FS19T8-3DPrinterBoard-STM32.kicad_pcb, appendix_SENSORS_POWER.sch]
2019-04-25 changed Layout to use all Interrupt Pins
    [FHNW-Pro4E-FS19T8-3DPrinterBoard-STM32.kicad_pcb, FHNW-Pro4E-FS19T8-3DPrinterBoard-STM32.sch, appendix_STM32F103.sch]
2019-04-25 fixed last minor issues
    [FHNW-Pro4E-FS19T8-3DPrinterBoard-STM32-B_Cu.gbr, FHNW-Pro4E-FS19T8-3DPrinterBoard-STM32-B_Mask.gbr, FHNW-Pro4E-FS19T8-3DPrinterBoard-STM32-B_Paste.gbr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]
2019-04-25 printed PDF and Gerbers
    [FHNW-Pro4E-FS19T8-3DPrinterBoard-STM32-B_Cu.gbr, FHNW-Pro4E-FS19T8-3DPrinterBoard-STM32-B_Mask.gbr, FHNW-Pro4E-FS19T8-3DPrinterBoard-STM32-B_Paste.gbr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]
2019-04-25 fixed minimum clearance of 0.125mm
    [FHNW-Pro4E-FS19T8-3DPrinterBoard-STM32-B_Cu.gbr, FHNW-Pro4E-FS19T8-3DPrinterBoard-STM32-B_Mask.gbr, FHNW-Pro4E-FS19T8-3DPrinterBoard-STM32-B_Paste.gbr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]
2019-04-25 increased size of USB Pad
    [FHNW-Pro4E-FS19T8-3DPrinterBoard-STM32.kicad_pcb, _saved_FHNW-Pro4E-FS19T8-3DPrinterBoard-STM32.sch]
2019-05-05 created assembly instructions
    [FHNW-Pro4E-FS19T8-3DPrinterBoard-STM32.kicad_pcb]
2019-05-10 added comments from comments branch corrected silk Servo2 added title to schematic pages
    [FHNW-Pro4E-FS19T8-3DPrinterBoard-STM32.kicad_pcb, FHNW-Pro4E-FS19T8-3DPrinterBoard-STM32.sch, appendix_ESP32.sch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]
2019-05-10 3d rendering + readme I probably broke the 3D rendering for others because of hardcoded paths to 3d shapes > works on my machine ¯\_(ツ)_/¯
    [FHNW-Pro4E-FS19T8-3DPrinterBoard-STM32.kicad_pcb]
2019-05-13 clarified some component values and printed PDFs
    [FHNW-Pro4E-FS19T8-3DPrinterBoard-STM32.kicad_pcb, FHNW-Pro4E-FS19T8-3DPrinterBoard-STM32.sch, appendix_SENSORS_POWER.sch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]
